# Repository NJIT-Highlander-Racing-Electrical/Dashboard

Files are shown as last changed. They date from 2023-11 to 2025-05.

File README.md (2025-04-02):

# 2024-2025 Dashboard

A dashboard for the vehicle including data from:
* CVT
* BajaDAS
* Wheel Speed Sensors

## 2024-2025 Design Goals

There are many aspects to improve on from last year's dashboard, as well as several other new features we would like to add. Here are some topics to look into:

* Sunshade
  * Last year, the LCDs were too dim in direct sunlight. This year, we will be implementing a sunshade to fix this
  * This sunshade can be made out of sheet metal, formed to shape with a 3D printed mold, attached via screws to the dashboard's back cover, and painted black to minimize reflections.
 * Improved front cover
     * The acrylic is subject to cracking under pressure from the mounting screws
     * This year, we will be using polycarbonate and we can use rubber washers on the mounting screws too
 * Waterproofing
     * Last year, the dashboard was not waterproof. This year, we are adding gasket material
          * For the front, we will sandwich it between the polycarbonate and 3D printed frame
          * For the rear, we can put it between the rear 3D printed cover and the main 3D printed frame
* Integration of wheel speed sensor data
     * Wheel speed data can be used to determine whether a wheel has locked up or has wheelspin.
     * This should be a bright color that takes priority over anything else on the dashboard. For example, if the front left wheel is locked, the top of the left circular display should flash red.
* Brighter Displays
     * With the dark mode background last year, the displays were not bright enough. This year we are using light backgrounds.
* Driver Input
     * This year, we are implementing two push buttons on the back of the dashboard that the driver can use
     * One button will enable/diasble data logging
     * The other button will start/stop a stopwatch
     * Pressing both buttons will send a flag bit to DAS and flash the screen
          * Acts as a data marker for certain things
          * Like a vehicle data "screenshot"
* Other limitations/setbacks are discussed in the [2023-2024 Archive README](https://github.com/NJIT-Highlander-Racing-Electrical/Dashboard/tree/main/2023-2024%20Archive)

## 2024-2025 Known Issues

### GC9A01 SCLK Pin

The SPI Clock pin on the ESP32 is 18, but the PCB has it tied to 19. On the final version, we can just snip off the two pins that go into the PCB and swap them around with two small jumpers. Software Serial is not ideal for speed and would require software modifications.

### TLC5917 Chip 3 OE and R-EXT Pins

On the TLC5917 that controls the green fuel LEDs, the R-EXT pin is tied to ground. This causes the TLC to try to push infinite current into the LEDs. We can simply not solder that pin to the pad, and instead bend it up and jump it to a GND pin using the proper resistor.

The OE pin has the resistor that should have been attached to the R-EXT pin. The OE pin needs to be pulled LOW to enable the displays, so we can simply short the resistor there to ground.

Update: It appears that the green LEDs at their fixed brightness (lack of functional OE pin) are way too bright. I am modifying the resistor value to 47000k, which is far less blinding

### Fuel LEDs

 The leftmost red LED does not light up in the boot animation

## Hardware

* ESP32 Microcontroller (Select NodeMCU-32S board in Arduino IDE)
* TJA1051T CAN Transceiver
* 1" Seven Segment Displays (Kingbright SA10-21SRWA)
* 1.28" Round LCDs
* 5mm LEDs
* TLC5917 8-Channel Sinking Constant Current LED Drivers

## Key Features

1. Real-Time Vehicle Speed Display
2. Analog Dial and Digital Output of CVT RPM
4. Digital CVT Ratio
5. Current Time (HH:MM:SS)
6. LED Indicators for Fuel Level
7. Status LEDs for CVT Temperature, Data Acquisition, Battery Level, and Power On/off
8. CAN-BUS Communication with Rest of Vehicle
9. Boot screen including Highlander Racing logo

## ESP32 Dual-Core Utilization

* We decided to run CAN-Bus scanning solely on Core 0 (via a task) to ensure all messages are properly received
* Writing to displays, 7-segment drivers, and math functions all take time, which means messages can be missed

## Visuals

* Includes a custom boot animation featuring the Highlander Racing logo and Lightning McQueen's number: 95
* RPM Visual comes from this repository: https://github.com/VolosR/TDisplayDashboard/tree/main
* At the competition, it was apparent that the whole dash was fairly dim in the bright sun
  * Goals for next year should be to incorporate an (ideally detachable) sunshade, brighter LEDs, brighter LCD displays or a suitable alternative
  * Other nice-to-haves would be a pot for brightness control and/or some other kind of driver input to change menus or settings
  * G-Force on driver indicator with magnitude and direction would be neat as well

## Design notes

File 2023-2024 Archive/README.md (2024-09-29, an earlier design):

# 2023-2024 Dashboard

Dashboard for the 2023 vehicle including data from:
* CVT
* Semi-Active Suspension
* Fuel Level Sensor
* BajaDAS
* 2WD/4WD Engagement Switch

## Setup Notes

If attempting to modify or upload the programs in this repository, make sure to utilize the libraries included. These libraries may have been modified from their default installations. For example, TFT_eSPI specifies default pins for CS and DC pins on the LCDs, but we have used different pins. 

Note that if you do not use these specific libraries, your PC may use any currently installed libraries at C:\Users\<USER_NAME>\Documents\Arduino\libraries, and this device may not function as intended.

## Hardware

* ESP32 Microcontroller (Select NodeMCU-32S board in Arduino IDE)
* TJA1051T CAN Transceiver
* 1" Seven Segment Displays (Kingbright SA10-21SRWA)
* 1.28" Round LCDs
* 5mm LEDs
* TLC5917 8-Channel Sinking Constant Current LED Drivers

## Key Features

1. Real-Time Vehicle Speed Display
2. Analog Dial and Digital Output of CVT RPM
3. Visual Indicator for 2WD/4WD Engagement
4. Digital CVT Ratio
5. Current Time (HH:MM:SS)
6. LED Indicators for Fuel Level
7. Status LEDs for CVT Temperature, Data Acquisition, Battery Level, and Power On/off
8. CAN-BUS Communication with Rest of Vehicle
9. Boot screen including Highlander Racing logo

## ESP32 Dual-Core Utilization

* We decided to run CAN-Bus scanning solely on Core 0 (via a task) to ensure all messages are properly received
* Writing to displays, 7-segment drivers, and math functions all take time, which means messages can be missed

## Visuals

* Includes a custom boot animation featuring the Highlander Racing logo and Lightning McQueen's number: 95
* RPM Visual comes from this repository: https://github.com/VolosR/TDisplayDashboard/tree/main
 
## Useful Sites
* TLC5917 Datasheet: https://www.ti.com/lit/ds/symlink/tlc5917.pdf?ts=1710497247983&ref_url=https%253A%252F%252Fgoogle.com
* 7-Segment Datasheet: http://www.us.kingbright.com/images/catalog/spec/SA10-21SRWA.pdf
* TLC5917 Library: https://github.com/Andy4495/TLC591x/tree/main
* Adafruit CAN Pal Guide: https://learn.adafruit.com/adafruit-can-pal/pinouts
* ESP32 Pinout: https://lastminuteengineers.com/wp-content/uploads/iot/ESP32-Pinout.png

 ## Known Issues/Limitations
 * The current PCB inside the dashboard has the fuel LEDs wire as follows
   * TLC Output -> LED Anode -> LED Cathode -> Current Limiting Resistor -> Ground
   * However, the TLC5917 is a sinking driver, and thus the LEDs need a 5V source
   * This issue should be fixed in the most up-to-date KiCad schematic and PCB
 * The density of the components and traces meant that seven traces could not be made without increasing the board thickness beyond two layers
   * To accomodate this, jumper wires were installed point to point to make the missing connections
 * The through holes for the LCDs and CAN-Bus module were too small and the headers had to be adjusted
 * The enclosure for the dashboard needs some improvements:
   * Better waterproofing (obviously)
   * Improved acrylic support
     * The front clear acrylic cover cracked due to the pressure from the bolts
* The DAS/battery subsystems do not include a method to obtain a low battery warning, so the battery light on the dashboard is not active
* The fuel sensor was not installed on the 2024 vehicle due to a lack of time, so the fuel LEDs are not active

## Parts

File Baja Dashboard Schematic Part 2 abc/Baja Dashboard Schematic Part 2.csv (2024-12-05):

Designator | Comment | Footprint
C1 | 10nF | Capacitor_Tantalum_SMD:CP_EIA-1608-08_AVX-J
C2 | 10^pF | Capacitor_Tantalum_SMD:CP_EIA-1608-08_AVX-J
C3,C4 | 10uF | Capacitor_Tantalum_SMD:CP_EIA-1608-08_AVX-J
LS1 | HMDZ Magnetic Buzzer 12x9.5mm 5V DC 85db with Pin | Buzzer_Beeper:Buzzer_12x9.5RM7.6
Q1 | MMBT2222_ | bajaRedoSaves:MMBT2222
R1 | 200 | Resistor_SMD:R_0201_0603Metric
R2,R3,R4,R5,R6,R7,R8,R9,R10,R11 | 300 | Resistor_SMD:R_0201_0603Metric
R12,R15,R16 | 1000 | Resistor_SMD:R_0201_0603Metric
R13,R14 | 750 | Resistor_SMD:R_0201_0603Metric
U1,U2,U3 | TLC5917 | bajaRedoSaves:TLC5917ID
U9 | TLC555xPS | bajaRedoSaves:TLC555

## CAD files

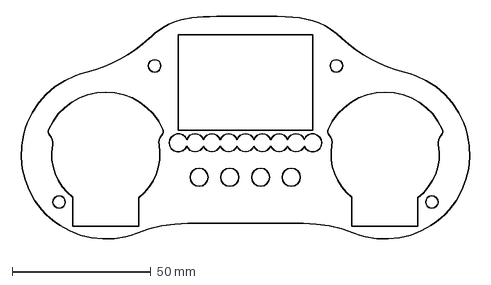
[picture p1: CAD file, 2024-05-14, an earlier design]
2023-2024 Archive/LaserCuts/Quarter Inch White Acrylic Outline.dxf
165.4 x 82.4 mm

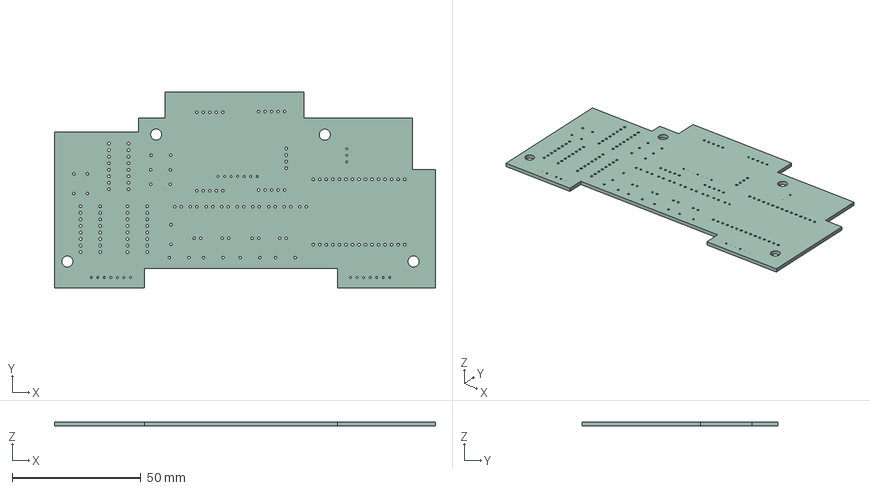
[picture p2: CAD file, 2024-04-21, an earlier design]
2023-2024 Archive/PCB/Baja Dashboard Schematic Part 2 abc/Baja Dashboard Schematic Part 2.step
148.0 x 76.0 x 1.60 mm

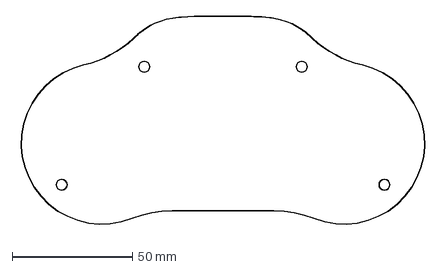
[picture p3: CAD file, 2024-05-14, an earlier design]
2023-2024 Archive/LaserCuts/Clear Acrylic Front Cover.dxf
172.0 x 88.8 mm

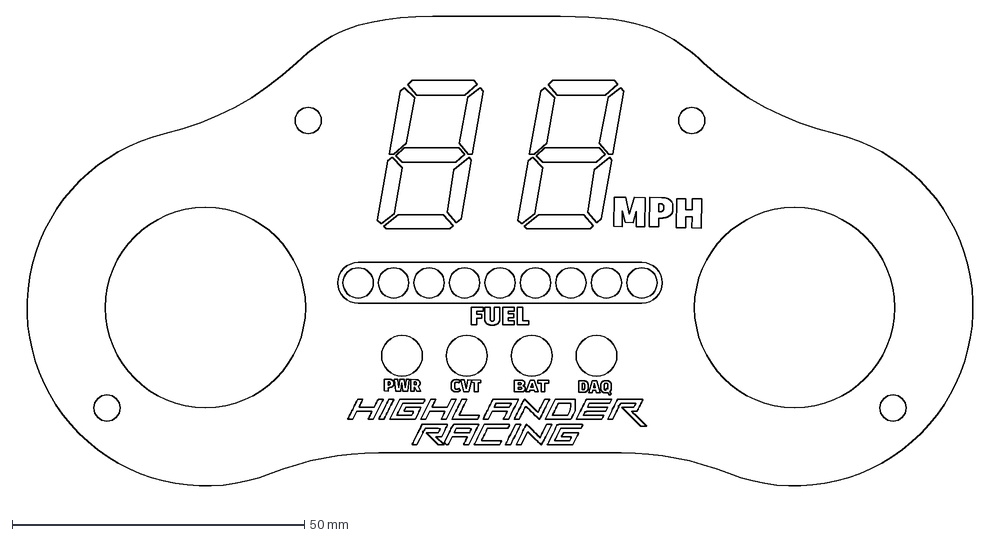
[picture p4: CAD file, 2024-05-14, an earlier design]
2023-2024 Archive/LaserCuts/Engraving Board v3.dxf
165.4 x 82.4 mm

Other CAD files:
3D Models/Previous Versions/Dashboard2025 v19.step
3D Models/Previous Versions/Dashboard2025 v19.f3z
3D Models/Previous Versions/Dashboard2025 v24.f3z

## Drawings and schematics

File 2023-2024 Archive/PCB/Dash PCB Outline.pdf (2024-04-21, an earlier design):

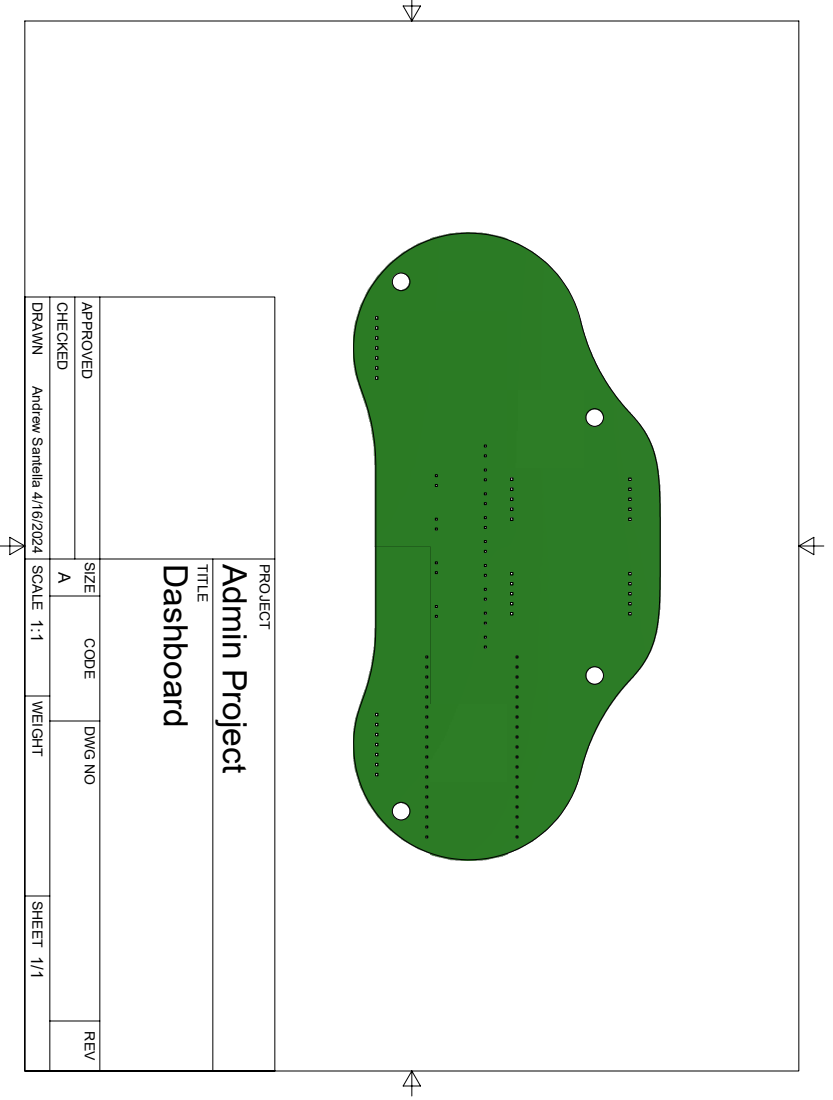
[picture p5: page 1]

TITLE PROJECT DRAWN CHECKED APPROVED SCALE WEIGHT SHEET DWG NO REV CODE SIZE 1/1 1:1 4/16/2024 Andrew Santella ADashboard Admin Project

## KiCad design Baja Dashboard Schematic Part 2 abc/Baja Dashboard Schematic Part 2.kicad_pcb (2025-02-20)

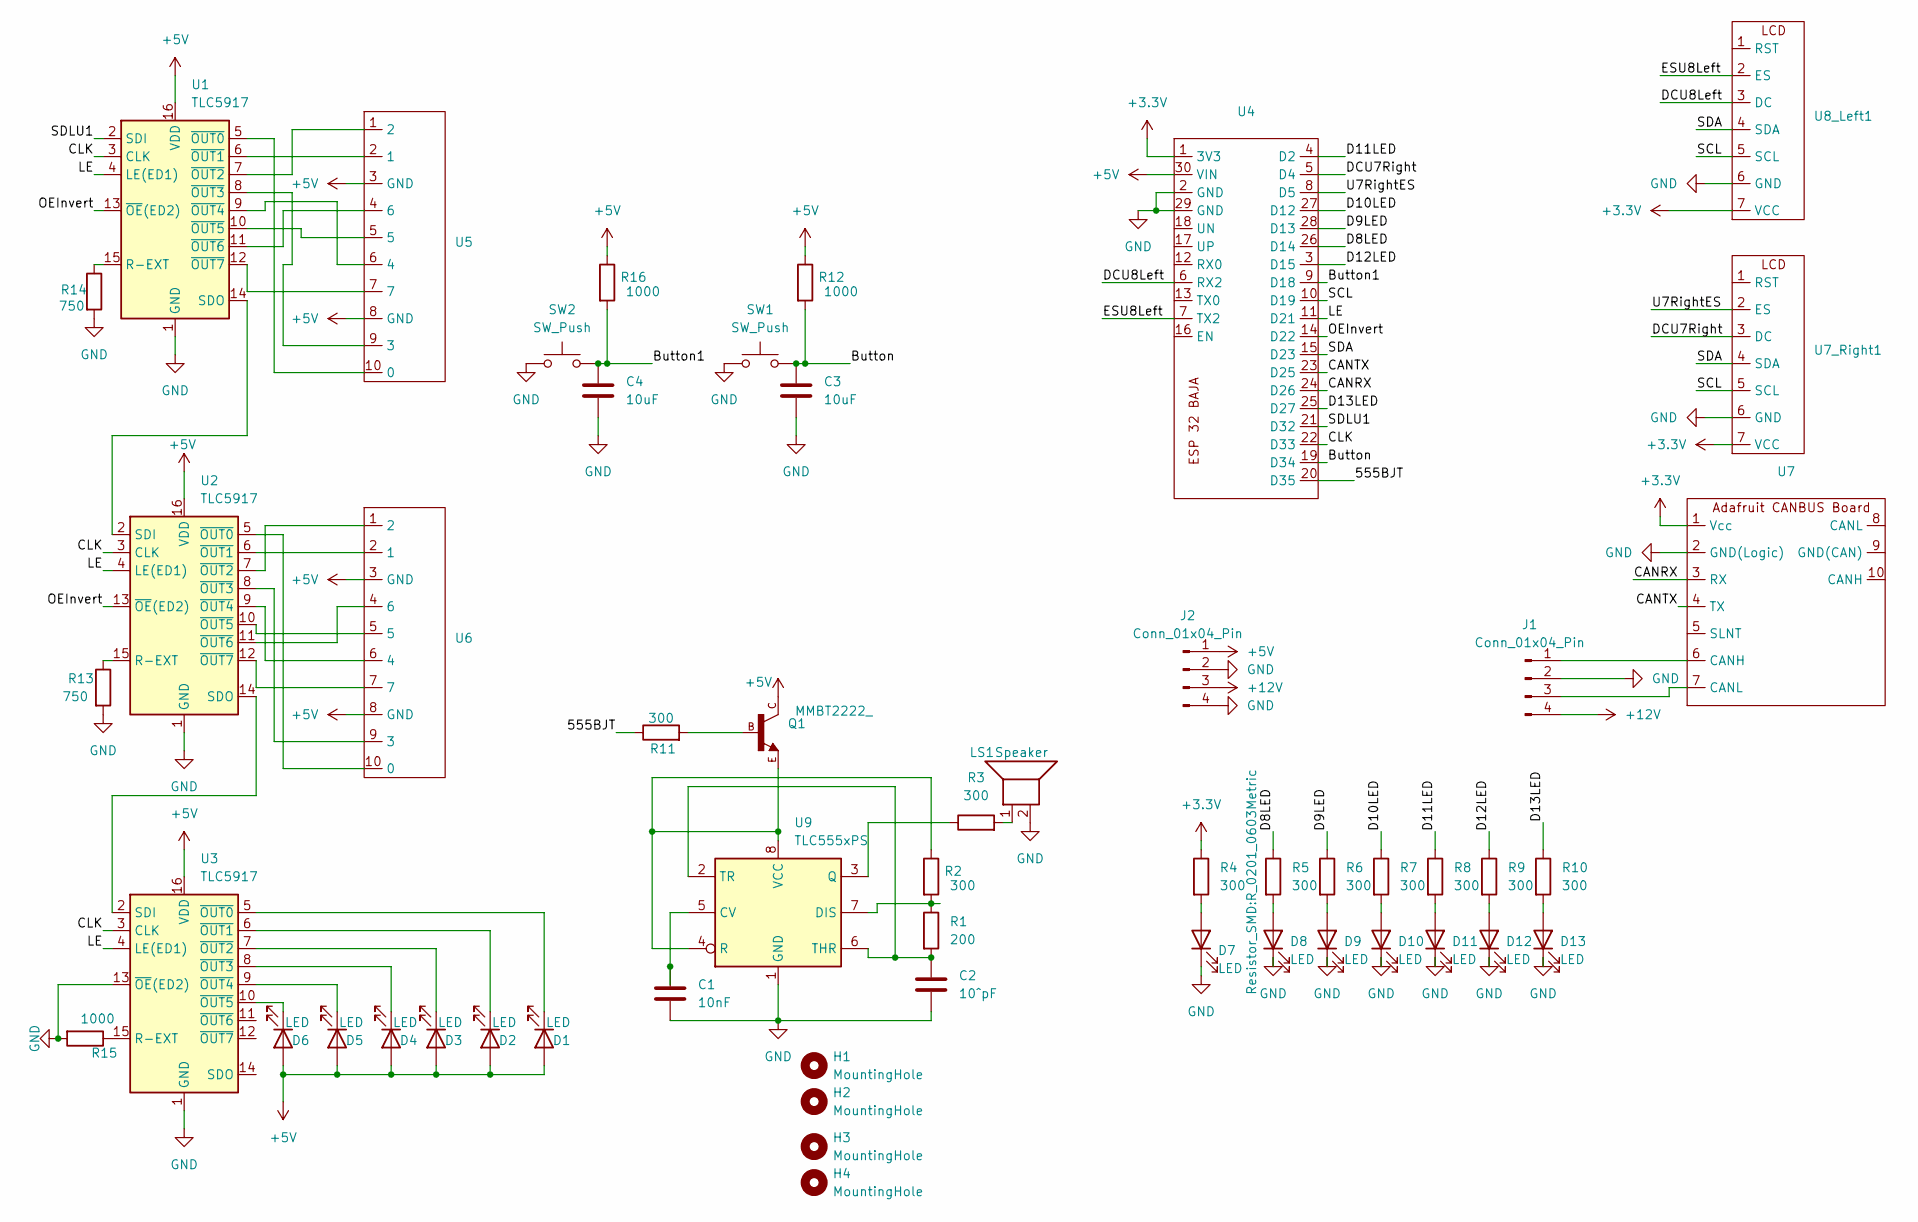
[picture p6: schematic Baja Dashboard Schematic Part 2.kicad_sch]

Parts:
C1: 10nF; CP_EIA-1608-08_AVX-J
C2: 10^pF; CP_EIA-1608-08_AVX-J
C3, C4: 10uF; CP_EIA-1608-08_AVX-J
D1, D2, D3, D4, D5, D6, D7, D8, D9, D10, D11, D12, D13: LED; LED 5mm Vertical
H1, H2, H3, H4: MountingHole; MountingHole_4.3mm_M4
J1: Conn_01x04_Pin
J2: Conn_01x04_Pin; PowerBoard
LS1: Speaker; Buzzer_12x9.5RM7.6
Q1: MMBT2222_; MMBT2222
R1: 200; R_0201_0603Metric
R2, R3, R4, R5, R6, R7, R8, R9, R10, R11: 300; R_0201_0603Metric
R12, R15, R16: 1000; R_0201_0603Metric
R13, R14: 750; R_0201_0603Metric
SW1, SW2: SW_Push; JST2pin
U1, U2, U3: TLC5917; TLC5917ID
U4: ESP 32 BAJA
U5, U6: baja 7 segment
U7, U7_Right1, U8_Left1: 1x7 Connectors
U9: TLC555xPS; TLC555

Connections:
+3.3V: R4.1, U4.1 (3V3), U7.1 (Vcc), U7_Right1.7 (VCC), U8_Left1.7 (VCC)
+5V: D1.2 (A), D2.2 (A), D3.2 (A), D4.2 (A), D5.2 (A), D6.2 (A), J2.1, Q1.C, R12.1, R16.1, U1.16 (VDD), U2.16 (VDD), U3.16 (VDD), U4.30 (VIN), U5.3 (GND), U5.8 (GND), U6.3 (GND), U6.8 (GND)
+12V: J1.4, J2.3
/555BJT: R11.1, U4.20 (D35)
/Button: C3.2, R12.2, SW1.2, U4.19 (D34)
/Button1: C4.2, R16.2, SW2.2, U4.9 (D18)
/CANRX: U4.24 (D26), U7.3 (RX)
/CANTX: U4.23 (D25), U7.4 (TX)
/CLK: U1.3 (CLK), U2.3 (CLK), U3.3 (CLK), U4.22 (D33)
/D8LED: R5.1, U4.26 (D14)
/D9LED: R6.1, U4.28 (D13)
/D10LED: R7.1, U4.27 (D12)
/D11LED: R8.1, U4.4 (D2)
/D12LED: R9.1, U4.3 (D15)
/D13LED: R10.1, U4.25 (D27)
/DCU7Right: U4.5 (D4), U7_Right1.3 (DC)
/DCU8Left: U4.6 (RX2), U8_Left1.3 (DC)
/ESU8Left: U4.7 (TX2), U8_Left1.2 (ES)
/LE: U1.4 (LE(ED1)), U2.4 (LE(ED1)), U3.4 (LE(ED1)), U4.11 (D21)
/OEInvert: U1.13 (~OE(ED2)), U2.13 (~OE(ED2)), U4.14 (D22)
/SCL: U4.10 (D19), U7_Right1.5 (SCL), U8_Left1.5 (SCL)
/SDA: U4.15 (D23), U7_Right1.4 (SDA), U8_Left1.4 (SDA)
/SDLU1: U1.2 (SDI), U4.21 (D32)
/U7RightES: U4.8 (D5), U7_Right1.2 (ES)
GND: C1.2, C2.2, C3.1, C4.1, D7.1 (K), D8.1 (K), D9.1 (K), D10.1 (K), D11.1 (K), D12.1 (K), D13.1 (K), J1.2, J2.2, J2.4, LS1.2, R13.2, R14.2, R15.2, SW1.1, SW2.1, U1.1 (GND), U2.1 (GND), U3.1 (GND), U3.13 (~OE(ED2)), U4.2 (GND), U4.29 (GND), U7.2 (GND(Logic)), U7_Right1.6 (GND), U8_Left1.6 (GND), U9.1 (GND)
unnamed: D1.1 (K), U3.5 (~OUT0)
unnamed: D2.1 (K), U3.6 (~OUT1)
unnamed: D3.1 (K), U3.7 (~OUT2)
unnamed: D4.1 (K), U3.8 (~OUT3)
unnamed: D5.1 (K), U3.9 (~OUT4)
unnamed: D6.1 (K), U3.10 (~OUT5)
unnamed: D7.2 (A), R4.2
unnamed: D8.2 (A), R5.2
unnamed: D9.2 (A), R6.2
unnamed: D10.2 (A), R7.2
unnamed: D11.2 (A), R8.2
unnamed: D12.2 (A), R9.2
unnamed: D13.2 (A), R10.2
unnamed: J1.1, U7.6 (CANH)
unnamed: J1.3, U7.7 (CANL)
unnamed: LS1.1, R3.2
unnamed: Q1.B, R11.2
unnamed: R14.1, U1.15 (R-EXT)
unnamed: U1.14 (SDO), U2.2 (SDI)
unnamed: U1.5 (~OUT0), U5.10 (0)
unnamed: U1.6 (~OUT1), U5.2 (1)
unnamed: U1.7 (~OUT2), U5.1 (2)
unnamed: U1.8 (~OUT3), U5.9 (3)
unnamed: U1.9 (~OUT4), U5.6 (4)
unnamed: U1.10 (~OUT5), U5.5
unnamed: U1.11 (~OUT6), U5.4 (6)
unnamed: U1.12 (~OUT7), U5.7
unnamed: R13.1, U2.15 (R-EXT)
unnamed: U2.14 (SDO), U3.2 (SDI)
unnamed: U2.5 (~OUT0), U6.10 (0)
unnamed: U2.6 (~OUT1), U6.2 (1)
unnamed: U2.7 (~OUT2), U6.1 (2)
unnamed: U2.8 (~OUT3), U6.9 (3)
unnamed: U2.9 (~OUT4), U6.6 (4)
unnamed: U2.10 (~OUT5), U6.5
unnamed: U2.11 (~OUT6), U6.4 (6)
unnamed: U2.12 (~OUT7), U6.7
unnamed: R15.1, U3.15 (R-EXT)
unnamed: C1.1, U9.5 (CV)
unnamed: R1.1, R2.2, U9.7 (DIS)
unnamed: R3.1, U9.3 (Q)
unnamed: Q1.E, R2.1, U9.4 (R), U9.8 (VCC)
unnamed: C2.1, R1.2, U9.2 (TR), U9.6 (THR)

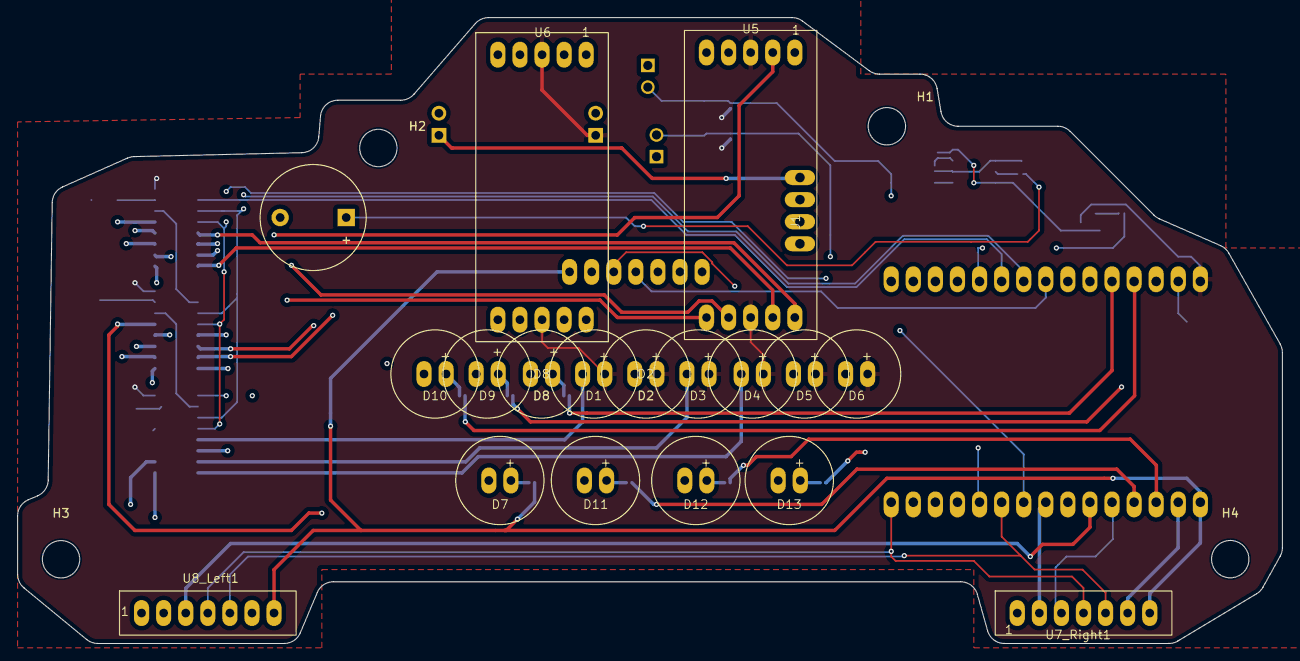
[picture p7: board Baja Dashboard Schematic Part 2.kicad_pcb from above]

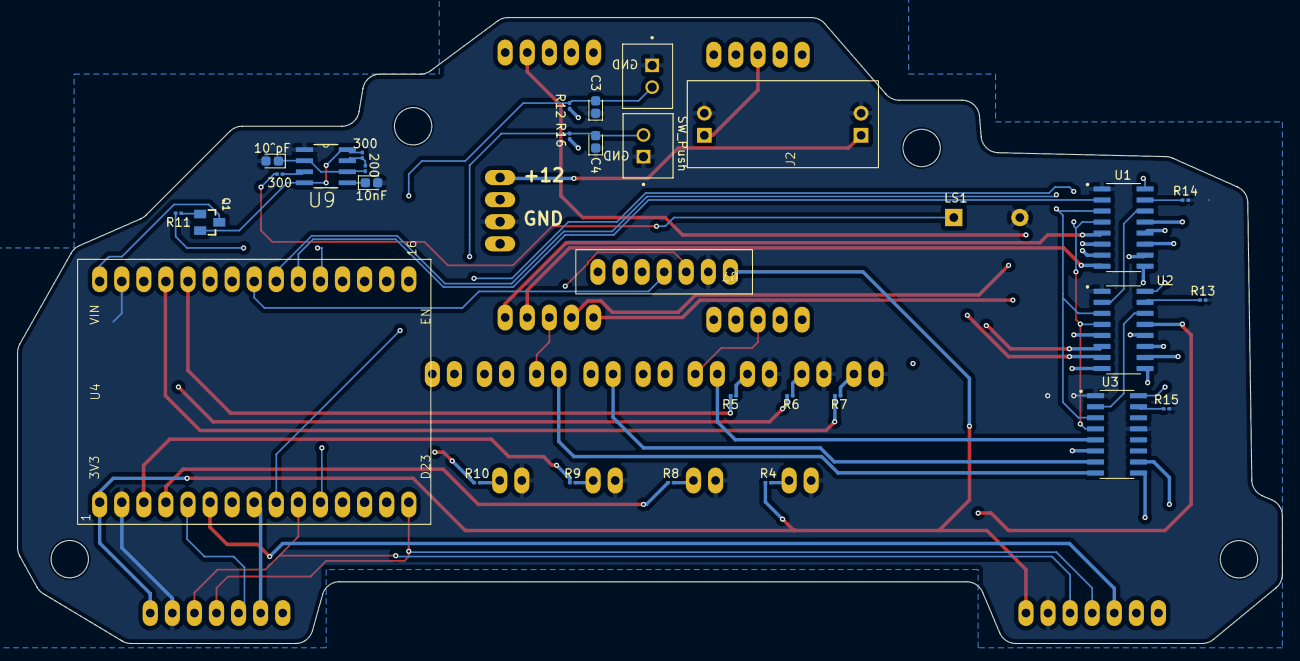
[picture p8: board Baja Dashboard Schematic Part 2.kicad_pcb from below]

Board: 4 copper layers, 145.5 x 72.0 mm, 53 parts (30 on the bottom side), 68 nets.

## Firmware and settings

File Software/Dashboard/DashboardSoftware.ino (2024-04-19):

// EXTREMELY IMPORTANT NOTE: THE FREQUENCY FOR THE CANBUS RATE IS DOUBLED ON THIS BECAUSE THE BOARDS ARE MESSED UP (WIDESPREAD ESP32 ISSUE)

#include <CAN.h>

TaskHandle_t CAN_Task;

#define DEBUG true
#define DEBUG_SERIAL \
  if (DEBUG) Serial

#define TX_GPIO_NUM 21  // Connects to CTX
#define RX_GPIO_NUM 22  // Connects to CRX

//#include <gpio_viewer.h>
//GPIOViewer gpio_viewer;

#include "SPI.h"
#include "Adafruit_GFX.h"
#include "Adafruit_GC9A01A.h"
#include <TJpg_Decoder.h>
#include <Fonts/FreeMono12pt7b.h>
#include <Fonts/FreeMonoBold18pt7b.h>
#include <Fonts/FreeMonoBold24pt7b.h>
#include <TLC591x.h>
#if defined(ENERGIA_ARCH_MSP432R)
#include <stdio.h>
#endif
TLC591x myLED(3, 32, 33, 25, 26);  // Uncomment if using OE pin

#include "rpmGauge.h"

// Setup for left circular display
#define TFT_DC_L 16
#define TFT_CS_L 17
Adafruit_GC9A01A tftL(TFT_CS_L, TFT_DC_L);

//X and Y positions on data on left circular display
const int timeHourX = 33;
const int timeMinuteX = 90;
const int timeSecondX = 150;
const int timeY = 60;
const int cvtRatioTextX = 100;
const int cvtRatioTextY = 180;
const int cvtRatioDataX = 80;
const int cvtRatioDataY = 220;
const int fourWheelX = 23;
const int fourWheelY = 130;
const int twoWheelX = 133;
const int twoWheelY = 130;

//Parameters to control the RPM dial on right circular display
const int cvtMinRPM = 0;
const int cvtMaxRPM = 4000;
const int angleMin = 0;
const int angleMax = 240;
int mappedRPMAngle = 0;


// Function for boot sequence Highlander Racing Image
bool tft_output(int16_t x, int16_t y, uint16_t w, uint16_t h, uint16_t* bitmap) {
  if (y >= tft.height()) return 0;
  tft.pushImage(x, y, w, h, bitmap);
  return 1;
}

//Defintions for CVT data (CVT RPM Sensor -> Dashboard Displays)
int primaryRPM = 0;
int secondaryRPM = 0;
float cvtMinRatio = 0.9;
float cvtMaxRatio = 3.9;
float cvtRatio = 0;
float lastCvtRatio = 0;
int lastRPM = 0;
const float gearboxRatio = 8.25;
const float wheelCircumference = 23.0;  //Wheel circumference in inches; distance traveled per revolution; should be 23 inches
float totalMultiplier = 0;
uint8_t wheelSpeed = 0;

//Number of fuel level LEDs to display (0-9)
int fuelLevel = 0;

//Definitions for four status LEDs
int cvtTemp = 0;
const int cvtTempMax = 150;
const int cvtOffTemp = 140;
bool daqOn = false;
bool daqError = false;
bool batteryLow = false;

//Pins for four status LEDs (power status is tied to VCC)
const int cvtLed = 2;
const int daqLed = 27;
const int batteryLed = 15;

//Pins for three non-green fuel LEDs (brightness was uneven with them on the LED driver :( )
const int redFuelLED = 12;
const int yellowFuelLED1 = 13;
const int yellowFuelLED2 = 14;

//Definitions for 2WD/4WD state
bool fourWheelsState = false;
bool lastFourWheelsState = false;
bool fourWheelsUnknown = true;
bool fourWheelsStartFlag = true;

int canbusDataPeriod = 50;
unsigned long canbusDataStart = 0;


//Definitions for GPS time
int timeH = 0;
int timeM = 0;
int timeS = 0;

int lastTimeH = 0;
int lastTimeM = 0;
int lastTimeS = 0;

unsigned long lastTimePingM = 0;
unsigned long lastTimePingS = 0;
bool hasBeenPinged = false;

//char formattedTime[9];

void setup() {

  DEBUG_SERIAL.begin(460800);
  //ESP32 MAC can be found using this: https://randomnerdtutorials.com/get-change-esp32-esp8266-mac-address-arduino/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
  //This one's is: D4:8A:FC:A8:59:7C
  //gpio_viewer.connectToWifi("SSID", "PASSWORD");
  //gpio_viewer.begin();



  CAN.setPins(RX_GPIO_NUM, TX_GPIO_NUM);

  if (!CAN.begin(1000E3)) {
    DEBUG_SERIAL.println("Starting CAN failed!");
    while (1)
      ;
  } else {
    DEBUG_SERIAL.println("CAN Initialized");
  }

  pinMode(cvtLed, OUTPUT);
  pinMode(daqLed, OUTPUT);
  pinMode(batteryLed, OUTPUT);
  pinMode(redFuelLED, OUTPUT);
  pinMode(yellowFuelLED1, OUTPUT);
  pinMode(yellowFuelLED2, OUTPUT);

  myLED.displayEnable();       // This command has no effect if you aren't using OE pin
  myLED.displayBrightness(0);  // 0 is max, 255 is min
  updateSevenSegments(95);     // Part of boot screen sequence

  TJpgDec.setSwapBytes(true);
  TJpgDec.setCallback(tft_output);
  rpmGaugeSetup();


  xTaskCreatePinnedToCore(
    CAN_Task_Code, /* Task function. */
    "CAN_Task",   /* name of task. */
    10000,     /* Stack size of task */
    NULL,      /* parameter of the task */
    1,         /* priority of the task */
    &CAN_Task,    /* Task handle to keep track of created task */
    0);        /* pin task to core 0 */
  delay(250);

  //Left display configurations
  tftL.begin();
  tftL.setFont(&FreeMonoBold24pt7b);
  tftL.fillScreen(GC9A01A_BLACK);

  //This should be a few seconds of splash screen displaying Highlander Racing logos/stuff on boot
  bootScreen();

  updateTime();
  totalMultiplier = (1.0 / gearboxRatio) * wheelCircumference * 3.1415926 * 0.00001578282828 * 60.0;  // 00001578282828 is miles in an inch
  updateCvtRatio();
  update2wd4wdState();
}



void loop() {

  cvtRatio = (secondaryRPM / (primaryRPM + 1.0));

  // 0.000015782828283 inches in a mile and 60 minutes in one hour
  wheelSpeed = (secondaryRPM * totalMultiplier);

  // This takes the calculated speed and displays it on the seven segments
  DEBUG_SERIAL.print("WHEEL SPEED: ");
  DEBUG_SERIAL.println(wheelSpeed);
  updateSevenSegments(wheelSpeed);

  //This takes the CVT rpm and plots the dial accordingly
  mappedRPMAngle = map(primaryRPM, cvtMinRPM, cvtMaxRPM, angleMin, angleMax);
  updateRPMGauge(mappedRPMAngle, primaryRPM);

  updateTime();

  //This updates the digital CVT ratio on left display
  if (abs(cvtRatio - lastCvtRatio) > 0.1) {
    lastCvtRatio = cvtRatio;
    updateCvtRatio();
  }

  //This updates the 2WD/4WD State on left display

  if (!fourWheelsUnknown && fourWheelsStartFlag) {
    fourWheelsStartFlag = false;
    lastFourWheelsState = fourWheelsState;
    update2wd4wdState();
  }

  if (fourWheelsState != lastFourWheelsState) {
    lastFourWheelsState = fourWheelsState;
    update2wd4wdState();
  }



  // These lines toggle the status LEDs
  if (batteryLow) digitalWrite(batteryLed, HIGH);
  else digitalWrite(batteryLed, LOW);

  if (daqOn && !daqError) {
    digitalWrite(daqLed, HIGH);
  } else if (daqError) {
    analogWrite(daqLed, 25);
  } else digitalWrite(daqLed, LOW);

  if (cvtTemp > cvtTempMax) digitalWrite(cvtLed, HIGH);
  if (cvtTemp < cvtOffTemp) digitalWrite(cvtLed, LOW);
}


void updateTime() {


  tftL.setFont(&FreeMonoBold18pt7b);
  tftL.setTextColor(TFT_WHITE);

  if (timeH != lastTimeH) {
    hasBeenPinged = true;
    lastTimeH = timeH;
    tftL.fillRect(timeHourX, timeY, (timeMinuteX - timeHourX), -(cvtRatioTextY - timeY), TFT_BLACK);
    tftL.setCursor(timeHourX, timeY);  // Adjust coordinates as needed
    if (timeH < 10) tftL.print("0");
    tftL.print(timeH);
    tftL.print(":");
  }

  if (timeM != lastTimeM) {
    lastTimePingM = millis();
    lastTimeM = timeM;
    tftL.fillRect(timeMinuteX, timeY, (timeSecondX - timeMinuteX), -(cvtRatioTextY - timeY), TFT_BLACK);
    tftL.setCursor(timeMinuteX, timeY);  // Adjust coordinates as needed
    if (timeM < 10) tftL.print("0");
    tftL.print(timeM);
    tftL.print(":");
  }
  if (((millis() - lastTimePingM) > 60000) && hasBeenPinged) {
    lastTimePingM = millis();
    timeM = timeM + 1;
    lastTimeM = timeM;
    tftL.fillRect(timeMinuteX, timeY, (240 - timeMinuteX), -(cvtRatioTextY - timeY), TFT_BLACK);
    tftL.setCursor(timeMinuteX, timeY);  // Adjust coordinates as needed
    if (timeM < 10) tftL.print("0");
    tftL.println(timeM);
  }

  if (timeS != lastTimeS) {
    lastTimePingS = millis();
    lastTimeS = timeS;
    tftL.fillRect(timeSecondX, timeY, (240 - timeSecondX), -(cvtRatioTextY - timeY), TFT_BLACK);
    tftL.setCursor(timeSecondX, timeY);  // Adjust coordinates as needed
    if (timeS < 10) tftL.print("0");
    tftL.println(timeS);
  }
  if (((millis() - lastTimePingS) > 1000) && hasBeenPinged) {
    lastTimePingS = millis();
    if (timeS > 59) {
      timeM++;
      timeS = 0;
    } else timeS++;
    lastTimeS = timeS;
    tftL.fillRect(timeSecondX, timeY, (240 - timeSecondX), -(cvtRatioTextY - timeY), TFT_BLACK);
    tftL.setCursor(timeSecondX, timeY);  // Adjust coordinates as needed
    if (timeS < 10) tftL.print("0");
    tftL.println(timeS);
  }
}

void updateCvtRatio() {

  tftL.fillRect(0, cvtRatioTextY, 240, 50, TFT_BLACK);
  tftL.setTextColor(TFT_WHITE);
  tftL.setCursor(cvtRatioTextX, cvtRatioTextY);  // Adjust coordinates as needed
  tftL.setFont(&FreeMono12pt7b);
  tftL.println("CVT");
  tftL.setFont(&FreeMonoBold24pt7b);
  tftL.setCursor(cvtRatioDataX, cvtRatioDataY);
  tftL.println(cvtRatio, 1);
}


void update2wd4wdState() {

  if (fourWheelsState && !fourWheelsUnknown) {

    tftL.fillRect(twoWheelX, twoWheelY, 240, 35, TFT_BLACK);
    tftL.setFont(&FreeMonoBold24pt7b);
    tftL.setTextColor(0x8410);
    tftL.setCursor(twoWheelX, twoWheelY);  // Adjust coordinates as needed
    tftL.println("2WD");
    tftL.setTextColor(TFT_RED);
    tftL.setCursor(fourWheelX, fourWheelY);  // Adjust coordinates as needed
    tftL.println("4WD");

  }

  else if (!fourWheelsState && !fourWheelsUnknown) {

    tftL.fillRect(twoWheelX, twoWheelY, 240, 35, TFT_BLACK);
    tftL.setFont(&FreeMonoBold24pt7b);
    tftL.setTextColor(TFT_RED);
    tftL.setCursor(twoWheelX, twoWheelY);  // Adjust coordinates as needed
    tftL.println("2WD");
    tftL.setTextColor(0x8410);
    tftL.setCursor(fourWheelX, fourWheelY);  // Adjust coordinates as needed
    tftL.println("4WD");
  }

  else {

    tftL.fillRect(twoWheelX, twoWheelY, 240, 35, TFT_BLACK);
    tftL.setFont(&FreeMonoBold24pt7b);
    tftL.setTextColor(0x8410);
    tftL.setCursor(twoWheelX, twoWheelY);  // Adjust coordinates as needed
    tftL.println("2WD");
    tftL.setTextColor(0x8410);
    tftL.setCursor(fourWheelX, fourWheelY);  // Adjust coordinates as needed
    tftL.println("4WD");
  }
}


//This is necessary to get a decimal number for the CVT ratio (standard MAP function will only return an int)
float mapfloat(long x, long in_min, long in_max, long out_min, long out_max) {
  return (float)(x - in_min) * (out_max - out_min) / (float)(in_max - in_min) + out_min;
}



void CAN_Task_Code( void * pvParameters ){
  Serial.print("CAN Task running on core ");
  Serial.println(xPortGetCoreID());

  for(;;){
 
 updateCanbus();  // dedicate 100ms to just canbus sampling to not miss messages
    delay(1);

  } 
}

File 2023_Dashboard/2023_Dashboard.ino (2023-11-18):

#include "SPI.h"
#include "Adafruit_GFX.h"
#include "Adafruit_GC9A01A.h"

#define TFT_DC_L 16
#define TFT_CS_L 17
Adafruit_GC9A01A tftL(TFT_CS_L, TFT_DC_L);

#include <Fonts/FreeMonoBold18pt7b.h>
#include <Fonts/FreeMonoBold24pt7b.h>

const int timeX = 30;
const int timeY = 60;
const int cvtRatioX = 85;
const int cvtRatioY = 150;
const int twoWheelX = 50;
const int twoWheelY = 220;
const int fourWheelX = 125;
const int fourWheelY = 220;



const int cvtMinRPM = 0;
const int cvtMaxRPM = 4000;
const int angleMin = 0;
const int angleMax = 240;

#define NEEDLE_LENGTH 45       // Visible length
#define NEEDLE_WIDTH 11        // Width of needle - make it an odd number
#define NEEDLE_RADIUS 95       // Radius at tip
#define NEEDLE_COLOR1 TFT_RED  // Needle periphery colour
#define NEEDLE_COLOR2 TFT_RED  // Needle centre colour
#define DIAL_CENTRE_X 120
#define DIAL_CENTRE_Y 120
#include "NotoSansBold36.h"
#define AA_FONT_LARGE NotoSansBold36
#include "dial.h"
#include <TFT_eSPI.h>
TFT_eSPI tft = TFT_eSPI();
TFT_eSprite needle = TFT_eSprite(&tft);  // Sprite object for needle
TFT_eSprite spr = TFT_eSprite(&tft);     // Sprite for meter reading
#include <TJpg_Decoder.h>
uint16_t* tft_buffer;
bool buffer_loaded = false;
uint16_t spr_width = 0;
uint16_t bg_color = 0;

bool tft_output(int16_t x, int16_t y, uint16_t w, uint16_t h, uint16_t* bitmap) {
  if (y >= tft.height()) return 0;
  tft.pushImage(x, y, w, h, bitmap);
  return 1;
}






// QUESTIONS FOR THIS PROJECT

// What voltage/current do the 7-segments need?
// Would this 8-bit shift register work? They can be daisy chained https://www.digikey.com/en/products/detail/texas-instruments/CD74HC597E/1507407
// How to interface TJA1051T with ESP32 TWAI Controller
// Keep a log of all libraries I use to upload with this code to GitHub!



int primaryRPM = 3000;
int secondaryRPM = 0;
float cvtMinRatio = 0.9;
float cvtMaxRatio = 3.9;
float cvtRatio = 0;
float lastCvtRatio = 0;
int lastRPM = 0;
const int gearboxRatio = 3;
int wheelSpeed = 0;

int fuelLevel = 0;

int cvtTemp = 0;
const int cvtTempMax = 100;
bool daqOn = false;
bool batteryLow = false;

const int cvtLed = 32;
const int daqLed = 33;
const int batteryLed = 25;

bool fourWheelsEngaged = false;
bool lastFourWheelsState = false;

int frontLeftWheel = 0;
int frontRightWheel = 0;
int rearLeftWheel = 0;
int rearRightWheel = 0;


//THESE CAN BE DELETED; JUST FOR TESTING PURPOSES
int switchTime = 2000;
int lastSwitchTime = 0;
const int CVT_TEST_POT = 15;

void setup() {

  Serial.begin(115200);

  pinMode(cvtLed, OUTPUT);
  pinMode(daqLed, OUTPUT);
  pinMode(batteryLed, OUTPUT);
  pinMode(CVT_TEST_POT, INPUT);


  TJpgDec.setSwapBytes(true);

  // The jpeg decoder must be given the exact name of the rendering function above
  TJpgDec.setCallback(tft_output);

  tft.begin();
  tft.setRotation(0);
  tft.fillScreen(TFT_BLACK);

  // Draw the dial
  TJpgDec.drawJpg(0, 0, dial, sizeof(dial));
  //tft.drawCircle(DIAL_CENTRE_X, DIAL_CENTRE_Y, NEEDLE_RADIUS-NEEDLE_LENGTH, TFT_DARKGREY);

  // Load the font and create the Sprite for reporting the value
  spr.loadFont(AA_FONT_LARGE);
  spr_width = spr.textWidth("7777");  // 7 is widest numeral in this font
  spr.createSprite(spr_width, spr.fontHeight());
  bg_color = tft.readPixel(120, 120);  // Get colour from dial centre
  spr.fillSprite(bg_color);
  spr.setTextColor(TFT_WHITE, bg_color, true);
  spr.setTextDatum(MC_DATUM);
  spr.setTextPadding(spr_width);
  spr.drawNumber(0, spr_width / 2, spr.fontHeight() / 2);
  spr.pushSprite(DIAL_CENTRE_X - spr_width / 2, DIAL_CENTRE_Y - spr.fontHeight() / 2);
  tft.setTextColor(TFT_WHITE, bg_color);
  tft.setTextDatum(MC_DATUM);
  tft.setPivot(DIAL_CENTRE_X, DIAL_CENTRE_Y);
  createNeedle();
  plotNeedle(0, 0);
  delay(500);



  tftL.begin();
  tftL.setFont(&FreeMonoBold18pt7b);
  tftL.setFont(&FreeMonoBold24pt7b);


  tftL.fillScreen(GC9A01A_BLACK);

  bootScreen();

  updateTime();
  updateCvtRatio();
  update2wd4wdState();

  //drawFourWheels();
}



void loop() {



  // Get CANBUS Data

  /*
*     FUEL GAUGE: 0-9 VALUE
*     2WD/4WD INPUT FROM DAQ
*     LOW BAT WARNING FROM DAQ
*     CVT PRIMARY/SECONDARY RPM FROM CVT
*     CVT RATIO FROM CVT
*     CVT OVER TEMP WARNING FROM CVT
*     
*/

  //

  daqOn = true;
  batteryLow = true;
  cvtTemp = 101;

  cvtRatio = mapfloat(analogRead(CVT_TEST_POT), 0.0, 4095.0, cvtMinRatio, cvtMaxRatio);
  if (analogRead(CVT_TEST_POT) > 2000) fourWheelsEngaged = true;
  else fourWheelsEngaged = false;
  primaryRPM = map(analogRead(CVT_TEST_POT), 0, 4095, cvtMinRPM, cvtMaxRPM);
  //

  int mappedAngle = map(primaryRPM, cvtMinRPM, cvtMaxRPM, angleMin, angleMax);
  if ((abs(primaryRPM - lastRPM)) > 50) {
    plotNeedle(mappedAngle, 1);  // if this doesnt work, add ms delay back to dial plot function
    lastRPM = primaryRPM;
  }

  if (false) {
    updateTime();
  }

  if (abs(cvtRatio - lastCvtRatio) > 0.1) {
    lastCvtRatio = cvtRatio;
    updateCvtRatio();
  }

  if (fourWheelsEngaged != lastFourWheelsState) {
    lastFourWheelsState = fourWheelsEngaged;
    update2wd4wdState();
  }





  if (batteryLow) digitalWrite(batteryLed, HIGH);
  else digitalWrite(batteryLed, LOW);

  if (daqOn) digitalWrite(daqLed, HIGH);
  else digitalWrite(daqLed, LOW);

  if (cvtTemp > cvtTempMax) digitalWrite(cvtLed, HIGH);
  else digitalWrite(cvtLed, LOW);
}


void updateTime() {

  tftL.fillRect(timeX, timeY, 240, -(cvtRatioY - timeY), TFT_BLACK);
  tftL.setFont(&FreeMonoBold18pt7b);
  tftL.setTextColor(TFT_WHITE);
  tftL.setCursor(timeX, timeY);  // Adjust coordinates as needed
  tftL.println("12:34:56");
}

void updateCvtRatio() {

  //cvtRatio = (primaryRPM / (secondaryRPM + 1));)
  tftL.fillRect(cvtRatioX, cvtRatioY, 240, -(twoWheelY - cvtRatioY), TFT_BLACK);
  tftL.setFont(&FreeMonoBold24pt7b);
  tftL.setTextColor(TFT_WHITE);
  tftL.setCursor(cvtRatioX, cvtRatioY);  // Adjust coordinates as needed
  tftL.println(cvtRatio, 1);
}


void update2wd4wdState() {

  if (fourWheelsEngaged) {

    tftL.fillRect(twoWheelX, twoWheelY, 240, -50, TFT_BLACK);
    tftL.setFont(&FreeMonoBold18pt7b);
    tftL.setTextColor(0x8410);
    tftL.setCursor(twoWheelX, twoWheelY);  // Adjust coordinates as needed
    tftL.println("2WD");
    tftL.setTextColor(TFT_RED);
    tftL.setCursor(fourWheelX, fourWheelY);  // Adjust coordinates as needed
    tftL.println("4WD");

  }

  else {

    tftL.fillRect(twoWheelX, twoWheelY, 240, -50, TFT_BLACK);
    tftL.setFont(&FreeMonoBold18pt7b);
    tftL.setTextColor(TFT_RED);
    tftL.setCursor(twoWheelX, twoWheelY);  // Adjust coordinates as needed
    tftL.println("2WD");
    tftL.setTextColor(0x8410);
    tftL.setCursor(fourWheelX, fourWheelY);  // Adjust coordinates as needed
    tftL.println("4WD");
  }
}
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

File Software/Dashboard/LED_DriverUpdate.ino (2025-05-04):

//A function that accepts an integer number (less than 99MPH) and configures each individual segment
//Once the proper segments are set, the displayData is written
//This also updated the battery LEDs using the global battery level variable

// Store the last battery level
int lastBatteryLevel = -1;  // Set an invalid initial value

// Define a hysteresis range (e.g., within 5 percentage points) (to eliminate flicker)
int hysteresisBuffer = 8;

void updateLedDisplays() {

  float slowestWheelSpeed = frontLeftWheelSpeed;
  if (frontRightWheelSpeed < frontLeftWheelSpeed) slowestWheelSpeed = frontRightWheelSpeed;
  if (rearLeftWheelSpeed < slowestWheelSpeed) slowestWheelSpeed = rearLeftWheelSpeed;
  if (rearRightWheelSpeed < slowestWheelSpeed) slowestWheelSpeed = rearRightWheelSpeed;


  uint8_t tens = slowestWheelSpeed / 10;   // Extract tens digit
  uint8_t units = (int)slowestWheelSpeed % 10;  // Extract units digit

  // Segment patterns for digits 0-9 on common-cathode displays
  const uint8_t segmentPatterns[] = {
    // abcdefg
    0b01111011,  // 0
    0b00110000,  // 1
    0b01101101,  // 2
    0b01110101,  // 3
    0b00110110,  // 4
    0b01010111,  // 5
    0b01011111,  // 6
    0b01110000,  // 7
    0b01111111,  // 8
    0b01110111   // 9
  };

  const uint8_t ledBarPatterns[] = {
    //Note: this function only controls the green LEDs
    0b00000000,  // 0
    0b00000000,  // 1
    0b00000000,  // 2
    0b00000000,  // 3
    0b10000000,  // 4
    0b11000000,  // 5
    0b11100000,  // 6
    0b11110000,  // 7
    0b11111000,  // 8
    0b11111100   // 9

  };

  // Update the number of LEDs based on the batteryPercentage
  updateBatteryLevel(batteryPercentage);

  // Calculate segment patterns for each digit
  uint8_t segmentsTens = segmentPatterns[tens];
  uint8_t segmentsUnits = segmentPatterns[units];
  uint8_t segmentsLedBar = ledBarPatterns[batteryLevel];


  // Display the speed and the green fuel LEDs using printDirect function
  uint8_t displayData[3] = { segmentsUnits, segmentsTens, segmentsLedBar };
  myLED.printDirect(displayData);

  //Update the other red and yellow fuel leds

  if (batteryLevel == 0) {
    digitalWrite(redLed, LOW);
    digitalWrite(yellowLed1, LOW);
    digitalWrite(yellowLed2, LOW);
  } else if (batteryLevel == 1) {
    digitalWrite(redLed, HIGH);
    digitalWrite(yellowLed1, LOW);
    digitalWrite(yellowLed2, LOW);
  } else if (batteryLevel == 2) {
    digitalWrite(redLed, HIGH);
    digitalWrite(yellowLed1, HIGH);
    digitalWrite(yellowLed2, LOW);
  } else {
    digitalWrite(redLed, HIGH);
    digitalWrite(yellowLed1, HIGH);
    digitalWrite(yellowLed2, HIGH);
  }
}


void updateBatteryLevel(int batteryPercentage) {
  int newBatteryLevel = 0;

  if (batteryPercentage < 20) newBatteryLevel = 1;
  else if (batteryPercentage < 30) newBatteryLevel = 2;
  else if (batteryPercentage < 40) newBatteryLevel = 3;
  else if (batteryPercentage < 50) newBatteryLevel = 4;
  else if (batteryPercentage < 60) newBatteryLevel = 5;
  else if (batteryPercentage < 70) newBatteryLevel = 6;
  else if (batteryPercentage < 80) newBatteryLevel = 7;
  else if (batteryPercentage < 90) newBatteryLevel = 8;
  else newBatteryLevel = 9;

  // Only update if the value has changed enough
  if (newBatteryLevel != lastBatteryLevel) {
    batteryLevel = newBatteryLevel;         // ✅ Assign it here!
    lastBatteryLevel = newBatteryLevel;
  }
}

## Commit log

2023-09-30 Create CAD-Model
2024-03-13 Rename Dashboard v37.step to 3D Models/Dashboard v37.step
    [Dashboard v37.step]
2024-04-04 Update and rename Clear Acrylic Front Cover.dxf to LaserCuts/Clear Acrylic Front Cover.dxf
    [Clear Acrylic Front Cover.dxf]
2024-04-10 Create KiCAD
2024-04-10 this is hte second one
    [Baja Dashboard Schematic Part 2-B_Cu.gbr, Baja Dashboard Schematic Part 2-B_Mask.gbr, Baja Dashboard Schematic Part 2-B_Paste.gbr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]
2024-04-21 reorganized all fines on desktop version
    [Baja Dashboard Schematic Part 2-B_Cu.gbr, Baja Dashboard Schematic Part 2-B_Mask.gbr, Baja Dashboard Schematic Part 2-B_Paste.gbr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]
2024-05-14 moving 2023-2024 files to archive
    [Baja Dashboard Schematic Part 2-B_Cu.gbr, Baja Dashboard Schematic Part 2-B_Mask.gbr, Baja Dashboard Schematic Part 2-B_Paste.gbr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]
2024-10-20 Update 23-24 Code For 24-25 Dash
    Note there is an issue with the TFT_eSPI library that prevents this program from compiling
    [Dashboard.ino, LED_DriverUpdate.ino, bootScreen.ino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]
2024-11-19 Rename Dashboard2025 v19.f3z to Dashboard2025 v19.f3z
    [Dashboard2025 v19.f3z]
2024-11-19 Rename Dashboard2025 v19.step to Dashboard2025 v19.step
    [Dashboard2025 v19.step]
2024-11-23 Move to 3D models folder
    [Dashboard2025 v24.f3z]
2024-12-04 New version with filleted edges
    [Baja Dashboard Schematic Part 2.kicad_pcb]
2024-12-05 Move previous versions to dedicated folder
    [Dashboard2025 v19.f3z, Dashboard2025 v19.step, Dashboard2025 v24.f3z]
2024-12-07 Add new GBR/DRL Files, Add new part position files
    [Baja Dashboard Schematic Part 2-bottom-pos.csv]
2024-12-15 Remove all Blind/Buried Vias for PCB manufacturing
    [Baja Dashboard Schematic Part 2.kicad_pcb]
2024-12-15 Fix top layer to bottom layers in component sheet
    [Baja Dashboard Schematic Part 2-all-pos-revised.csv]
2024-12-18 Fix blind/buried via on LE trace
    [Baja Dashboard Schematic Part 2.kicad_pcb]
2025-02-06 Attempt to move libraries to project folder
    I spent lots of time trying to incorporate all of these libraries into a single project folder, but Arduino doesn't like this. Since most of the libraries are written with references to files like this <File.h>, it will not look in our project's src/libraries folder. If I get it working, great, otherwise the default Arduino's library folder will have to suffice
    [Dashboard.ino]
2025-02-06 Move back to regular arduino library folder
2025-02-12 Revert back to Arduino IDE libraries
    Everything now uses libraries stored in Arduino/libraries folder. Code was updated to use variables stored in BajaCAN.h, still have to check if there are other variables that are redefined and need to be migrated to BajaCAN.h
    [Dashboard.ino, bootScreen.ino, rpmGauge.h]
2025-02-12 Add libraries
    These are copied from my Documents/Arduino/libraries folder on my laptop, from which I got a successful upload using V2.0.17 ESP32 in board manager. Not sure if everything is exactly correct, as the LCDs are not active, but the code does compile and the 7-segments work. Some modifications to these libraries may be necessary
2025-02-12 ???
    This should have been uploaded with my previous commit regarding using Documents/Arduino/libraries, not sure why it didnt complete
2025-02-12 Update 5mm LED GPIO pin values for new PCB
2025-02-12 Update 5mm LED Pin numbers again; PCB pin names are inconsistent with ESP32 GPIO
2025-02-12 Fix D8 and D2 silkscreen on wrong layer
    [Baja Dashboard Schematic Part 2.kicad_pcb]
2025-02-12 Remove debug print statement and decrease 7-segment brightness for testing
2025-02-20 fixed PCB
    Fixed pin 15 issue
    [Baja Dashboard Schematic Part 2-B_Cu.gbr, Baja Dashboard Schematic Part 2-B_Mask.gbr, Baja Dashboard Schematic Part 2-B_Paste.gbr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]
2025-02-20 Changes to UI
    White background
    black text
    timer is set to 04:55:55 as a test, comment it out and uncomment the main function code
2025-03-02 Updated screen options
    Changed from calculated speed for mph to gpsvelocity
    Implemented gpsvelocity for wheel traction and locked wheel indicator lights
    implemented brightness control
    implemented data marker
    Started error code screen
    [Dashboard.ino, rpmGauge.h]
2025-03-08 Finished implementing button controls
    Vomited if statements. Screw you, I'm not optimizing the code. Nothing mechanical is dependent on electrical systems.
2025-03-29 Added elapsed time and made fixes
    [Dashboard.ino, rpmGauge.h]
2025-03-29 Update to latest BajaCAN.h driver
2025-03-29 See Changelog
    Renamed all fuel related variables to ledBar or batteryLevel or just Led for clarity
    Added comments to various functions
    Removed unused code for calculating vehicle speed from CVT secondary RPM (using GPS Velocity)
    Cleaned up loop() function
    Fixed spelling
    Modified variable names to be consistent with camelCase
    [Dashboard.ino, LED_DriverUpdate.ino, bootScreen.ino]
2025-03-29 See Changelog
    Revised variable names for clarity
    Move most code in loop() into individual functions
    Add more comments
    Remove unused code (2WD/4WD switch, etc)
2025-04-01 Major Updates
    Update wheelspin/skid code to use data sent from Wheel Speed sensors instead of calculating its own
    Categorize code before setup()
    Remove unused variables
    Convert all serial prints to debug prints
    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
2025-04-01 Update both programs to use lower color depth on right display
    I believe the color depth was defaulting to 16 bit, which meant that the ESP32 could not handle full screen rendering. It was limited to roughly 235x235, so there were weird cutoffs to the round disp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
2025-04-01 Experimenting with Adafruit Canvas Updating
    Stopwatch with milliseconds caused severe display flicker. Using their Canvas function, you can generate a whole bitmap and push that to the display at once to eliminate flicker. Only downside is not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
2025-04-01 Fix position of stopwatch
    [Alternative_Display_Program.ino]
2025-04-02 Update to lates CAN Driver
2025-04-12 Fixed the RPM gauge and buttons
    [Dashboard.ino]
2025-04-13 Fix DAQ Led not resetting, Fix RPM dial position
    [Dashboard.ino, rpmGauge.h]
2025-04-13 Fix bug where red fuel led would not light
    This happened because TFT_eSPI was somehow latching onto pin 12 and making it something other than an output. This was after we had declared it as an output earlier in the code, so when we go to use it later on, it just dont work
    [Dashboard.ino, rpmGauge.h]
2025-04-13 Fix sd logging/stopwatch/screenshot button presses and fix battery led flicker
    [Dashboard.ino, LED_DriverUpdate.ino]
2025-05-03 Update to latest CAN, start using lowest wheel speed for vehicle speed
2025-05-03 I think this fixed the CAN not working issue
    [Dashboard.ino]
2025-05-03 Fix LED bar not working
    [LED_DriverUpdate.ino]
2025-05-04 Latest Code, was working with PCAN, ensured that termination resistor was active
2025-05-04 Remove wheel spin skid screens, werent working properly
2025-05-10 Attempt to fix dashboard CAN not working issue
    Only works when code is uploaded from laptop
    When booted on without laptop, does not work
    still works when laptop unplugged after uploading code
    [Dashboard.ino]
2025-05-11 Fix bug where stopwatch was overwriting gps time
    [Dashboard.ino]
2025-05-11 Actually fixing bug from before
    [Dashboard.ino]
2025-06-13 Fix odometer and add delay for CAN initializatoin
    [Dashboard.ino]
2025-06-13 fix cvt ratio printing over for odometer, attempt to fix intermitten can startup
    [Dashboard.ino]
2025-06-13 Attempt to fix odometer creeping up over time even at 0 speed
    [Dashboard.ino]
2025-06-13 make sure no gps velocity results in odometer creep up
2025-06-13 Update odometer to use wheel speed for more accuracy
2025-06-14 Flip buttnons for better usability (more logical)
    [Dashboard.ino]
